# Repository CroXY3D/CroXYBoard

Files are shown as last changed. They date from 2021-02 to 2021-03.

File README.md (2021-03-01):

# CroXYBoard
CroXYBoard is a small 36x34mm toolboard for simplifying 3D printer tool wiring.  It is used on the CroXY and MicroXY printers.  

_It was developed from the ground up, but shares some similarities with the [Carabiner](https://github.com/Kirinkunhime/Annex_Engineering_PCBs/tree/master/carabiner-toolboard) board._

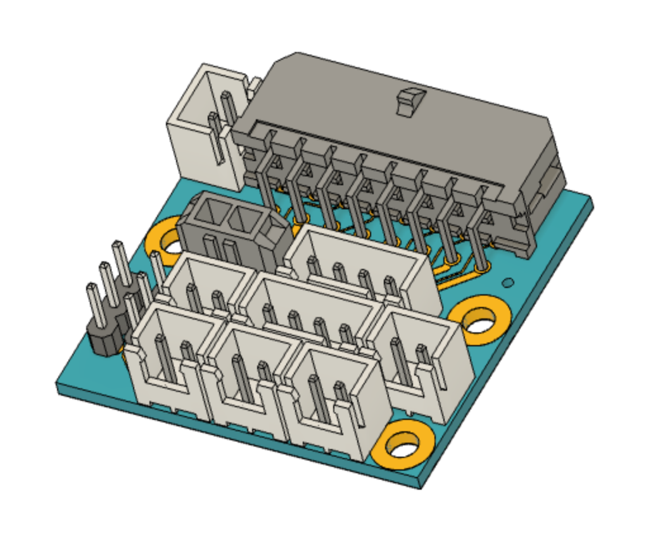
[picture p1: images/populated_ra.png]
right angle

Right Angle Connector
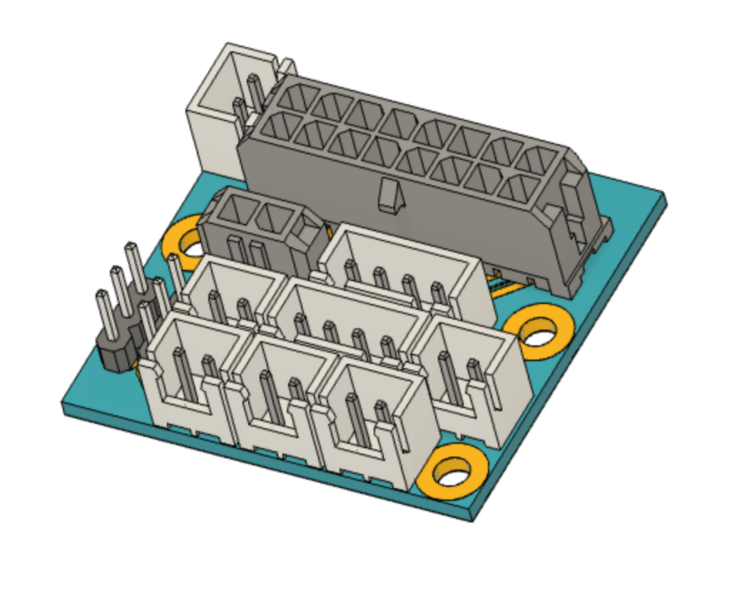
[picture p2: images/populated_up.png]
upright

Upright Connector
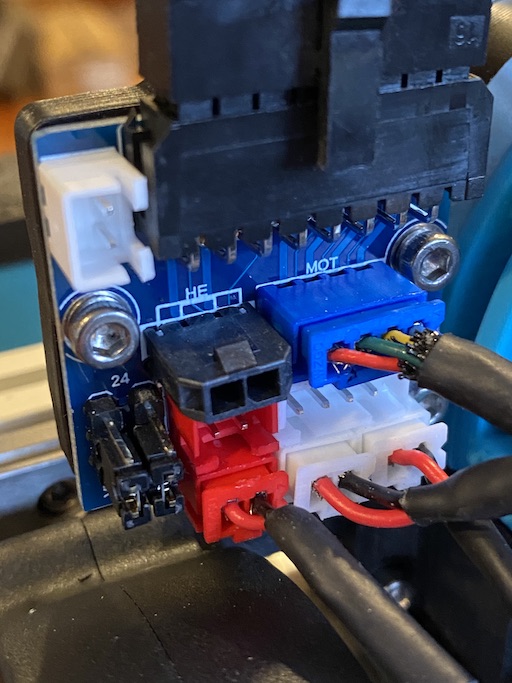
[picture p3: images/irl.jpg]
IRL


This toolboard uses a 16 pin Microfit 3.0 connector and provides XH connections at the toolhead for:
* Extruder
* Hot End (Microfit 3.0 or XH)
* Thermistor
* Hot End Fan (12/24V selectable)
* Part Cooling Fan x2 (12/24V selectable)
* Switch - for endstop or other use
* Aux - 3 more connections for BLTouch or other use
* LED - Always on (12/24V selectable via trace cut/jump).  This may be used as a generic power source.

It is possible to use 2 CroXYBoards with one near the printer's controller board and the other at the toolboard.  This may simplify wiring somewhat.  

# 16 PIN MOLEX PIN ASSIGNMENTS

Note that the pre-wired 16p cable reuses colors.  You will have to trace out which is which.  I mark 9-16 with a bit of heatshrink.

1 (Yellow) 12V - If using 24V fans, this can be connected to 24V or left disconnected

2 (Brown) GND

3 (Purple) THERMISTOR A

4 (Blue) THERMISTOR B

5 (Green) SWITCH - XH connector has GND as the other pin.

6 (White) AUX1 - 4th pin of the AUX connector is GND.

7 (Black) AUX2

8 (Red) AUX3

9 (Yellow) 24V

10 (Brown) HOTEND LOW SIDE - High side is connected to 24V

11 (Purple) HOTEND FAN LOW SIDE - High side is jumper selectable

12 (Blue) PARTCOOLING FAN LOW SIDE - High Side is jumper selectable

13 (Green) MOTOR 1

14 (White) MOTOR 2

15 (Black) MOTOR 3

16 (Red) MOTOR 4

# BOM  
* 1x PCB (See Below)
* 1x 16 pin Microfit3 board connector.  [Right angle Molex 43045-1600](https://www.digikey.com/en/products/detail/molex/0430451600/531424) or [Upright Molex 43045-1612](https://www.digikey.com/en/products/detail/molex/0430451612/531412).
* 1x [2 pin Microfit3 upright board connector - Molex 43650-0227](https://www.digikey.com/en/products/detail/molex/0436500227/3310541?s=N4IgTCBcDaICwGYBsBWADAWjWMB2EAugL5A)
* 2x [4 pin XH connectors - JST B4B-XH-A](https://www.digikey.com/en/products/detail/jst-sales-america-inc/B4B-XH-A-LF-SN/1651047)
* 6x [2 pin XH connectors - JST B2B-XH-A](https://www.digikey.com/en/products/detail/jst-sales-america-inc/B2B-XH-A-LF-SN/1651045)
* 2x [3 pin jumper headers - Molex 22032031](https://www.digikey.com/en/products/detail/molex/0022285034/6167122) (optional, may solder jumper instead)
* 2x [2 pin jumpers AMP 861410021H11LF](https://www.digikey.com/en/products/detail/amphenol-icc-fci/861410021H11LF/4417821) (optional, may solder jumper instead)
* 1x 16 pin [Microfit3 receptacle - Molex 43025-1600](https://www.digikey.com/en/products/detail/molex/0430251600/531406), or [prewired 16 pin microfit cable harness](https://www.aliexpress.com/item/4001132970645.html?spm=a2g0s.9042311.0.0.27424c4d12p2WJ) (recommended)

# PCB Manufacturing
I recommend [JLCPB](http://https://jlcpcb.com/) for getting the boards made inexpensively and efficiently.
[OshPark](https://oshpark.com/) is another option.
You only need to upload the gerbers zip file.

# DISCORD
We now have a [Discord](https://discord.gg/ryj6wyx) to discuss CroXYBoard and CroXY!

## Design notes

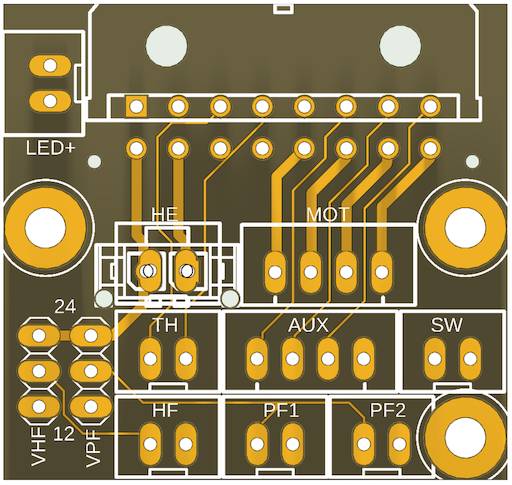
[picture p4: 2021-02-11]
images/front_sm.png

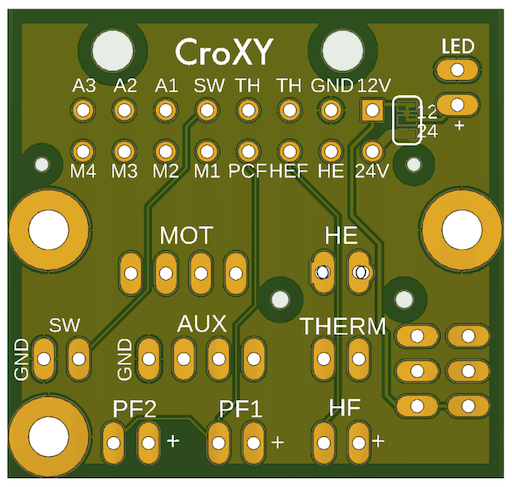
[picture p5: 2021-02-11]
images/back_sm.png

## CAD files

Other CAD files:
fusion/Toolboard v101.f3z

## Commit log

2021-02-11 V 1.0
    [Toolboard v101.f3z]
2021-02-11 BOM update
2021-02-11 bom fix
